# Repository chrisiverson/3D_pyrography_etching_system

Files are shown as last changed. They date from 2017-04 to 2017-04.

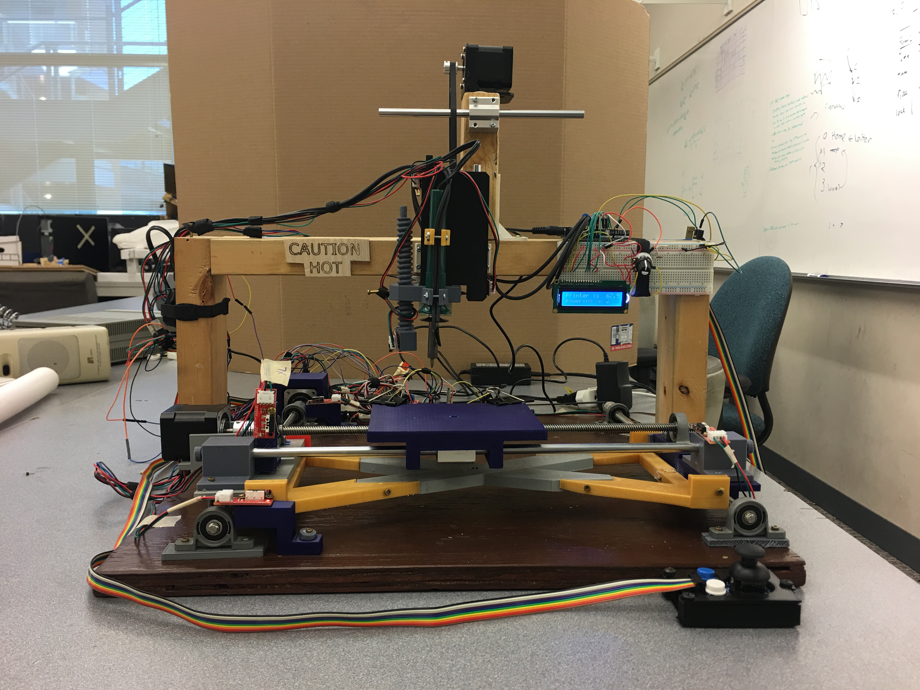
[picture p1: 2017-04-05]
Pictures/IMG_1217.JPG

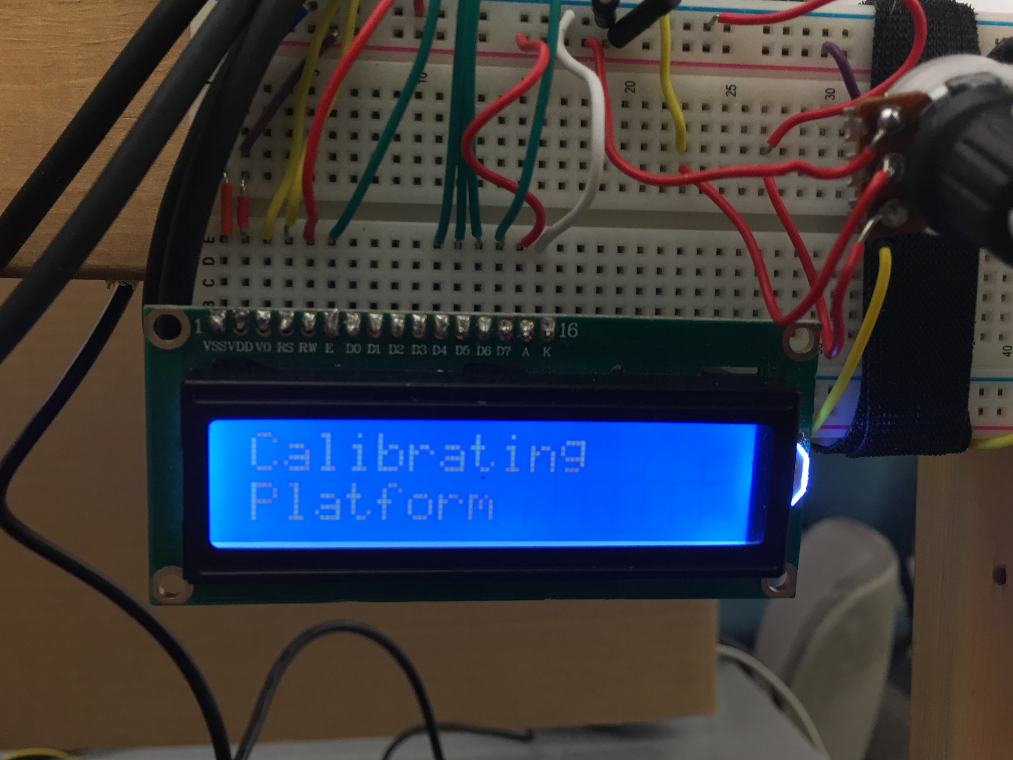
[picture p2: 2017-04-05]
Pictures/IMG_1232.JPG

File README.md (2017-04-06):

# 3D_pyrography_etching_system

3.P.E.S is a pyrography etching system. This system is capable of wood burning an image that the  user manually engraves via a joystick or sends to our machine via a smartphone application. The reason  we designed this system is because of our interest in 3-D printing. We wanted to take an artistic and unique approach to implementing an x, y, z theta platform.

Video demo: https://www.youtube.com/watch?v=G6UNE0NW478

This project falls under creative copyrights to 

Christopher Iverson
chris.iverson.ee@gmail.com

Dineth Gamalath
dinethgamalath@gmail.com

Steven Hernandez
stevenhdz@gmail.com

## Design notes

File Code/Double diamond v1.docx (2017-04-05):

/*

2-axis joystick connected to an Arduino Micro

to output 4 pins, up, down, left & right

If you are using pull down resistors, change all the HIGHs to LOWs and LOWs to HIGH.

This skectch is using pull up resistors.

*/

String readString;

int UD = 0;

int LR = 0;

/* Arduino Micro output pins*/

int DWN = 27;

int UP = 29;

int LEFT = 31;

int RT = 33;

/* Arduino Micro Input Pins */

int IUP=59;//A5

int ILR=63;//A9

int MID = 33; // 33 mid point delta arduino, use 4 for attiny

int LRMID = 0;

int UPMID = 0;

char randomflag = 0;

const int x_endstopPin_min = 3; // endstop for x-axis (min)

const int x_endstopPin_max = 2; // endstop for x-axis (max)

const int y_endstopPin_min = 14; // endstop for y-axis (min)

const int y_endstopPin_max = 15; // endstop for y-axis (max)

const int z_endstopPin = 18; //endstop for z-axis

const int buttonPin = 47; //D47 // the number of the pushbutton pin

const int buttonPin2 = 32; //D32

const int ledPin = 23; // the number of the LED pin

int buttonState = 0; // variable for reading the pushbutton status

int buttonState2 = 0;

int x_endstopState_min = 0; //these states will contain value from reading input values

int x_endstopState_max = 0;

int y_endstopState_min = 0;

int y_endstopState_max = 0;

int z_endstopState = 0;

int XL = 0;

int XR = 0;

int YU = 0;

int YD = 0;

int ZU = 0;

int ZD = 0;

int XL1 = 1000;

int XR1 = 0;

int YU1 = 0;

int YD1 = 1000;

int ZU1 = 0;

int ZD1 = 0;

int XL2 = 0;

int XR2 = 1000;

int YU2 = 0;

int YD2 = 1000;

int ZU2 = 0;

int ZD2 = 0;

int XL3 = 1000;

int XR3 = 0;

int YU3 = 0;

int YD3 = 1000;

int ZU3 = 0;

int ZD3 = 0;

int XL4 = 0;

int XR4 = 1000;

int YU4 = 0;

int YD4 = 1500;

int ZU4 = 0;

int ZD4 = 0;

int XL5 = 0;

int XR5 = 1000;

int YU5 = 1000;

int YD5 = 0;

int ZU5 = 0;

int ZD5 = 0;

int XL6 = 1000;

int XR6 = 0;

int YU6 = 1000;

int YD6 = 0;

int ZU6 = 0;

int ZD6 = 0;

int XL7 = 0;

int XR7 = 1000;

int YU7 = 1000;

int YD7 = 0;

int ZU7 = 0;

int ZD7 = 0;

int XL8 = 1000;

int XR8 = 0;

int YU8 = 1000;

int YD8 = 0;

int ZU8 = 0;

int ZD8 = 0;

int XLEND = 0;

int XREND = 0;

int YUEND = 0;

int YDEND = 0;

int ZUEND = 0;

int ZDEND = 0;

int Done = 1;

int move_num = 0;

void mover()

{

Done = 0;

XL = XL1;

XR = XR1;

YU = YU1;

YD = YD1;

ZU = ZU1;

ZD = ZD1;

XL1 = XL2;

XR1 = XR2;

YU1 = YU2;

YD1 = YD2;

ZU1 = ZU2;

ZD1 = ZD2;

XL2 = XL3;

XR2 = XR3;

YU2 = YU3;

YD2 = YD3;

ZU2 = ZU3;

ZD2 = ZD3;

XL3 = XL4;

XR3 = XR4;

YU3 = YU4;

YD3 = YD4;

ZU3 = ZU4;

ZD3 = ZD4;

XL4 = XL5;

XR4 = XR5;

YU4 = YU5;

YD4 = YD5;

ZU4 = ZU5;

ZD4 = ZD5;

XL5 = XL6;

XR5 = XR6;

YU5 = YU6;

YD5 = YD6;

ZU5 = ZU6;

ZD5 = ZD6;

XL6 = XL7;

XR6 = XR7;

YU6 = YU7;

YD6 = YD7;

ZU6 = ZU7;

ZD6 = ZD7;

XL7 = XL8;

XR7 = XR8;

YU7 = YU8;

YD7 = YD8;

ZU7 = ZU8;

ZD7 = ZD8;

XL8 = XLEND;

XR8 = XREND;

YU8 = YUEND;

YD8 = YDEND;

ZU8 = ZUEND;

ZD8 = ZDEND;

move_num++;

return;

}

void setup(){

Serial.begin(9600);

pinMode(ledPin, OUTPUT);

// initialize the pushbutton pin as an input:

pinMode(buttonPin, INPUT);

pinMode(x_endstopPin_min, INPUT);

pinMode(x_endstopPin_max, INPUT);

pinMode(y_endstopPin_min, INPUT);

pinMode(y_endstopPin_max, INPUT);

pinMode(z_endstopPin, INPUT);

pinMode(DWN, OUTPUT);

pinMode(UP, OUTPUT);

pinMode(LEFT, OUTPUT);

pinMode(RT, OUTPUT);

digitalWrite(DWN, HIGH);

digitalWrite(UP, HIGH);

digitalWrite(LEFT, HIGH);

digitalWrite(RT, HIGH);

//calabrate center

LRMID = analogRead(ILR);

UPMID = analogRead(IUP);

pinMode(38, OUTPUT); //Enable X // old 6

pinMode(54, OUTPUT); //Step X // old 5

pinMode(55, OUTPUT); //Direction // old 4

pinMode(56, OUTPUT);// Enable Y

pinMode(60, OUTPUT);// Step Y

pinMode(61, OUTPUT);// Direction Y

//digitalWrite(38,LOW);

pinMode(62, OUTPUT);// Enable Z

pinMode(46, OUTPUT);// Step Z

pinMode(48, OUTPUT);// Direction Z

}

void loop(){

while (Serial.available()) {

delay(3);

char c = Serial.read();

readString += c;

}

//***********************************BLUETOOTH BEGIN*****************

if (readString.length() >0) {

Serial.println(readString);

if(readString == "UP")

{

randomflag = 1;

}

else if (readString == "off")

{

randomflag = 0;

}

readString="";

}

//***********************************BLUETOOTH END*******************

x_endstopState_min = digitalRead(x_endstopPin_min); //this obtains the "1" or "0" from endstop signal

x_endstopState_max = digitalRead(x_endstopPin_max);

y_endstopState_min = digitalRead(y_endstopPin_min);

y_endstopState_max = digitalRead(y_endstopPin_max);

z_endstopState = digitalRead(z_endstopPin);

buttonState = digitalRead(buttonPin);

buttonState2 = digitalRead(buttonPin2);

UD = analogRead(IUP);

LR = analogRead(ILR);

//z-direction button UP

int buttonvar = buttonState;

int buttonvar2 = buttonState2;

int x_endstopvar_min = x_endstopState_min;

int x_endstopvar_max = x_endstopState_max;

int y_endstopvar_min = y_endstopState_min;

int y_endstopvar_max = y_endstopState_max;

int z_endstopvar = z_endstopState;

if (!buttonvar)

{

// turn LED on:

digitalWrite(48,LOW);//direction

digitalWrite(46,HIGH);//step

digitalWrite(46,LOW);//step

delayMicroseconds(200);

}

else if(buttonvar)

{

digitalWrite(46,LOW);

}

if (!buttonvar2 && z_endstopvar)

{

// turn LED on:

digitalWrite(ledPin, HIGH);

// Serial.println("LED on");

digitalWrite(48,HIGH);//direction

digitalWrite(46,HIGH);//step

digitalWrite(46,LOW);//step

delayMicroseconds(200);

}

else if(buttonvar || buttonvar2)

{

digitalWrite(46,LOW);

}

if (Done && (move_num < 9))

{

mover();

}

if ( XR == 0 && XL == 0 && YU == 0 && YD == 0)

{

//Serial.println("TESTEHRFSB");

Done = 1;

}

// y-direction UP

if((((UD < UPMID - MID) || (randomflag ==1)) || (YU > 0)) && y_endstopvar_min ){

digitalWrite(DWN, LOW);

digitalWrite(61,LOW);

digitalWrite(UP, LOW);

digitalWrite(60,HIGH);

delayMicroseconds(200);

YU--;

}

else

{

digitalWrite(DWN, HIGH);

digitalWrite(60,LOW);

}

// y-direction DOWN

if(((UD > UPMID + MID) || (YD > 0)) && y_endstopvar_max ){

digitalWrite(UP, LOW);

digitalWrite(61,HIGH);

//digitalWrite(DWN, LOW);

digitalWrite(60,HIGH);

delayMicroseconds(200);

YD--;

}

else

{

digitalWrite(UP, HIGH);

digitalWrite(60,LOW);

}

// LEFT-RIGHT

//x-direciton LEFT

if(((LR < LRMID - MID) || (XL > 0)) && x_endstopvar_max ){// min

digitalWrite(55,LOW);

//digitalWrite(LEFT, LOW);// LEDS

digitalWrite(54,HIGH);

delayMicroseconds(200);

XL--;

}

else{

digitalWrite(54,LOW);

digitalWrite(LEFT, HIGH);

}

//x-direction RIGHT

if(((LR > LRMID + MID) || (XR > 0)) && x_endstopvar_min ){

digitalWrite(55,HIGH);

//digitalWrite(RT, LOW);

digitalWrite(54,HIGH);

delayMicroseconds(200);

XR--;

}else{

digitalWrite(54,LOW);

digitalWrite(RT, HIGH);

}

/*

//x-direciton LEFT

if(LR < LRMID - MID){

digitalWrite(48,LOW);

digitalWrite(LEFT, LOW);

digitalWrite(46,HIGH);

delayMicroseconds(200);

}

else{

digitalWrite(46,LOW);

digitalWrite(LEFT, HIGH);

}

//x-direction RIGHT

if(LR > LRMID + MID){

digitalWrite(48,HIGH);

digitalWrite(RT, LOW);

digitalWrite(46,HIGH);

delayMicroseconds(200);

}else{

digitalWrite(46,LOW);

digitalWrite(RT, HIGH);

}

*/

//delay(200);

}

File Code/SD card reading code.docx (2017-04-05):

File dataFile = SD.open("Strip3_5.txt"); if (datafile) { for (index = 0; index <= 9; index++) { int input = datafile.parseInt(); String3_5[index] = input; Serial.println(input); } file.close(); }

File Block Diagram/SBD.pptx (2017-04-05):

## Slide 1

System Block Diagram for EDWARD

Drill / Soldering Attachment / Pen

End Stops / Sensors

Arduino 1

Arduino Shield Driver Board + Driver

X – Direction Stepper Motor

Joystick

Y – Direction Stepper Motor

Z – Direction Stepper Motor

Application

Wireless Communication Module

Arduino 2

Voltage & Power Controller

Display Unit

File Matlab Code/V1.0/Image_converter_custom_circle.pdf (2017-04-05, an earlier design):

clc
clear all
close all

Im_name = 'custom.png';
Im = imread(Im_name);
Im_size(:)=size(Im);%Gather size data of image X=Im_size(1);%Save the x dimension Y=Im_size(2);%Save the Y dimension

while Y > 300
Im = imresize(Im,.5);
Im_size(:)=size(Im);%Gather size data of image X=Im_size(1)%Save the x dimension Y=Im_size(2)%Save the Y dimension
end

X = 450
Y = 481
X = 225
Y = 241

histogram(Im)

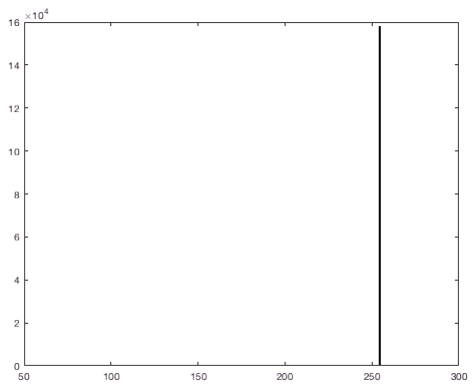
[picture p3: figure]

%Add or remove thresholds in the line below according to the histogram %Globe threshs: 0,117,200
thresh = [117,200]

thresh =

117 200

%Convert the image based on the thresholds Im_Shaded = imquantize(Im,thresh);

%fileID = fopen('Untitled.txt','wt'); %fprintf(fileID,'%f',Im_Shaded); %fclose(fileID);

imshow(Im);

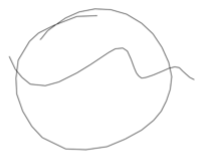
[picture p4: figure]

histogram(Im)

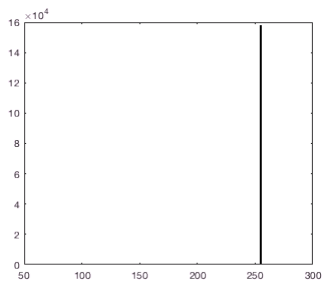
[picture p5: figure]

histogram(Im_Shaded)

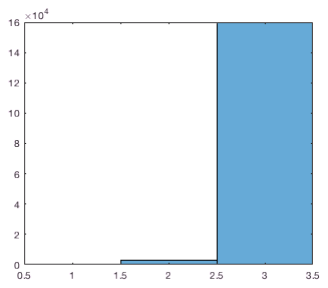
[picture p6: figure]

imshow(Im_Shaded,[])

%Now isolating each shade as a seperate b and w image max_value=max(Im_Shaded(:))

max_value = 3

Im_array_1=im2bw(Im,thresh(1)/255); Im_array_2=~im2bw(Im,thresh(2)/255); Im_array_3=im2bw(Im,thresh(2)/255);

imshow(Im_array_1);

imshow(Im_array_2);

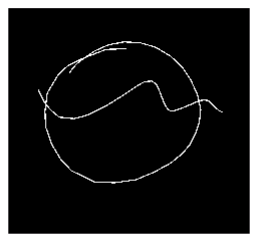
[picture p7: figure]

imshow(Im_array_3);

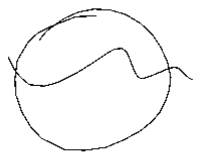
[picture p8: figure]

%-------------------------------------------num_objects_1 = max(max(bwlabel(Im_array_1)))

num_objects_1 = 1

num_objects_2 = max(max(bwlabel(Im_array_2)))

num_objects_2 = 1

num_objects_3 = max(max(bwlabel(Im_array_3)))

num_objects_3 = 1

%Converts the different shades into outlines
Im_array_outline_3 = bwmorph(Im_array_3,'remove');
Im_array_outline_2 = (bwmorph(bwmorph(Im_array_2,'remove'),'clean'));
Im_array_outline_1 = bwmorph(Im_array_1,'remove')-bwmorph(Im_array_3,'remove')-bwmorph(Im_array_2,'remove');

imshow(Im_array_outline_1)

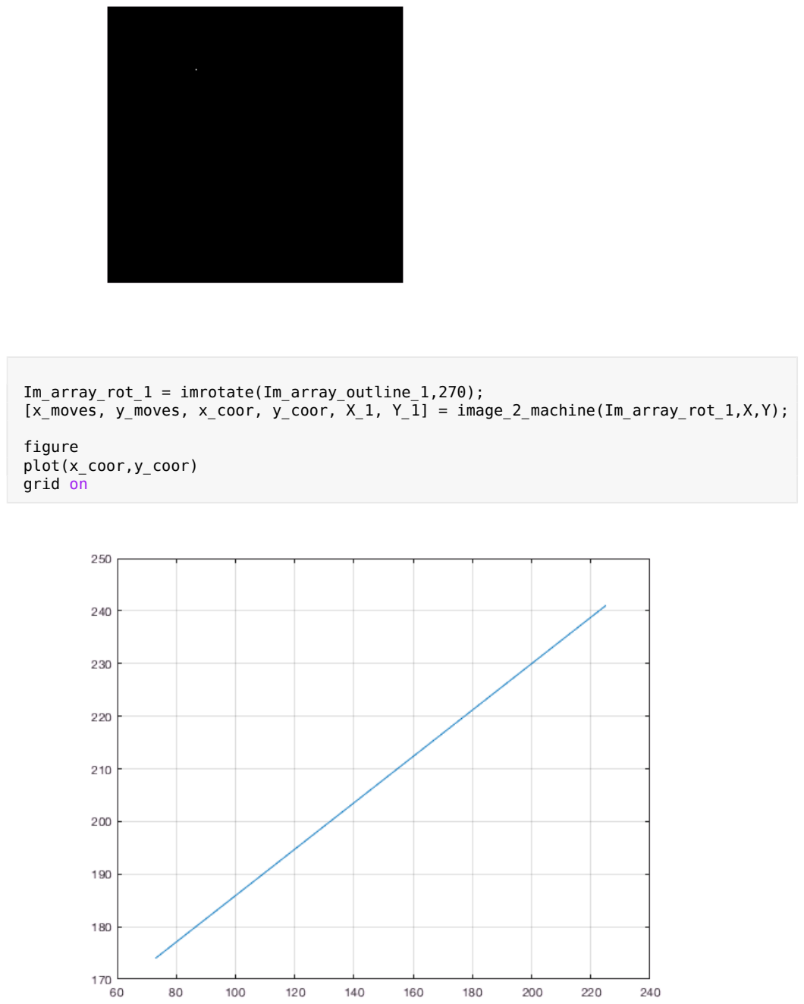
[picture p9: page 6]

Im_array_rot_1 = imrotate(Im_array_outline_1,270);
[x_moves, y_moves, x_coor, y_coor, X_1, Y_1] = image_2_machine(Im_array_rot_1,X,Y);

figure
plot(x_coor,y_coor)
grid on

Im_please_work = Im_array_1 - Im_array_3 - Im_array_outline_2;

imshow(Im_please_work)

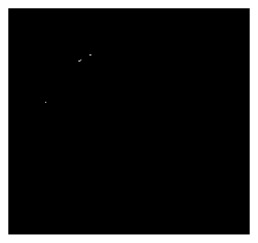
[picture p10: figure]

Im_array_rot_1 = imrotate(Im_please_work,270);
[x_moves_2, y_moves_2, x_coor_2, y_coor_2, X_2, Y_2] = image_2_machine(Im_array_rot_1,X_1,Y_1);

figure
plot(x_coor_2,y_coor_2)
grid on

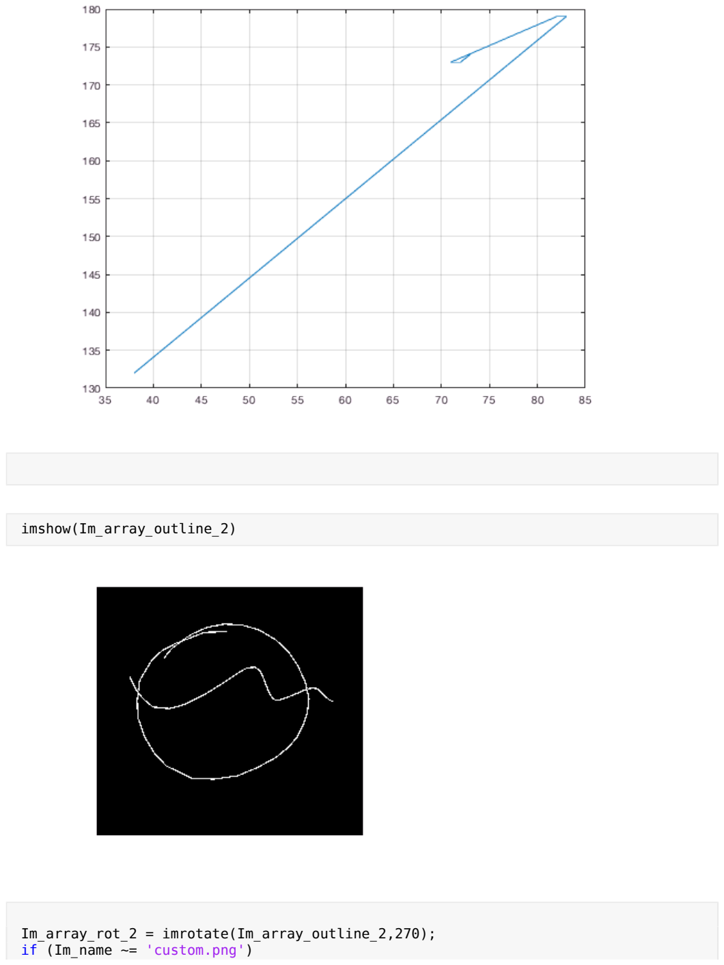
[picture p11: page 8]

imshow(Im_array_outline_2)

Im_array_rot_2 = imrotate(Im_array_outline_2,270); if (Im_name ~= 'custom.png')

[x_moves_3, y_moves_3, x_coor_3, y_coor_3, X_3, Y_3] = image_2_machine(Im_array_rot_2,X_2,Y_2); else
[x_moves_3, y_moves_3, x_coor_3, y_coor_3, X_3, Y_3] = image_2_machine(Im_array_rot_2,1,1); end

figure
plot(x_coor_3,y_coor_3)
grid on

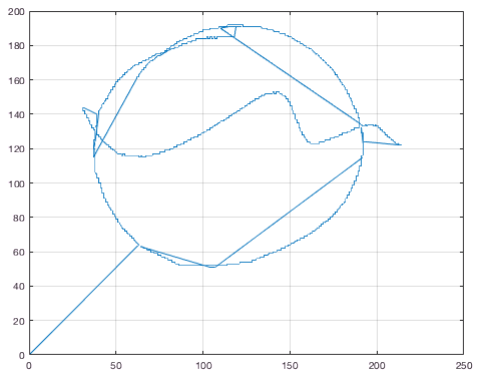
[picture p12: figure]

Im_please_work_2 = Im_array_2-Im_array_1;

imshow(Im_please_work_2)

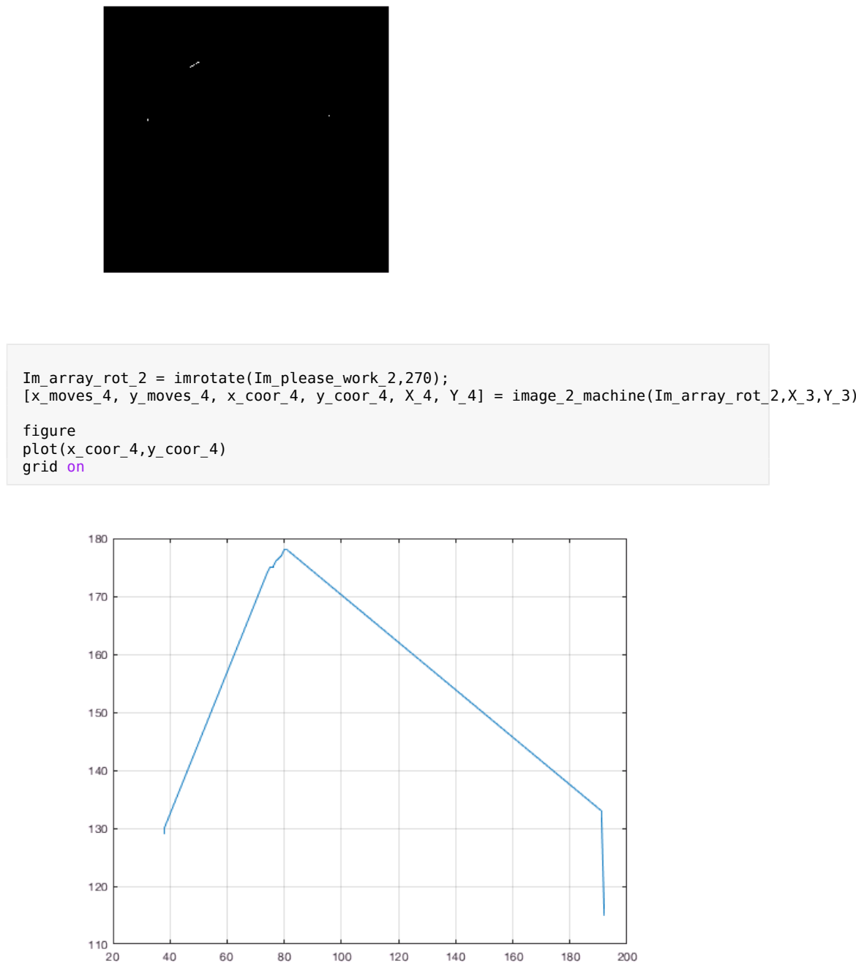
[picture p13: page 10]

Im_array_rot_2 = imrotate(Im_please_work_2,270);
[x_moves_4, y_moves_4, x_coor_4, y_coor_4, X_4, Y_4] = image_2_machine(Im_array_rot_2,X_3,Y_3);

figure
plot(x_coor_4,y_coor_4)
grid on dec2bin(abs(y_moves_3(1)),8);

%[x_move_3, y_move_3, final_x_3, final_y_3, num_steps_3 ] = conv_to_moves( Im_array_outline_1, final_x_2, final_y_2);

if (Im_name ~= 'custom.png')
num_steps = length(x_moves_4)+length(x_moves_3)+length(x_moves_2)+length(x_moves)

fileID = fopen('image_data.h','w');
fprintf(fileID,'long num_of_steps = ');
fprintf(fileID,'%1i;\n\n',num_steps);
fprintf(fileID,'//Coordinates: \n//'); for i = 1:length(x_coor_3)
if x_coor_3(i) < 0
fprintf(fileID,'%1i',0-x_coor_3(i)); else
fprintf(fileID,'%1i',x_coor_3(i)); end
fprintf(fileID,',');
if y_coor_3(i) < 0
fprintf(fileID,'%1i',0-y_coor_3(i)); else
fprintf(fileID,'%1i',y_coor_3(i)); end
if (num_steps ~= i)

fprintf(fileID,',');
end
end

fprintf(fileID,'\n//Move list from origin (0,0) with every 4 numbers being a step: \n//'); for i = 1:length(x_moves_3)
if x_moves_3(i) < 0
fprintf(fileID,' %1i, 0',0-x_moves_3(i));
else
fprintf(fileID,' 0, %1i',x_moves_3(i)); end
fprintf(fileID,',');
if y_moves_3(i) < 0
fprintf(fileID,' %1i, 0',0-y_moves_3(i)); else
fprintf(fileID,' 0, %1i',y_moves_3(i)); end
if (num_steps ~= i)

fprintf(fileID,';');
end
end
fprintf(fileID,'\n//Binary move list with 3 moves per byte\n//Format: 0x00,Move1,Move2,Move3\n//Example: 0x00110010 = 0x00,UR,DL,UL\n'); fprintf(fileID,'byte move_list[] = {');

write_2_file(x_moves_3,y_moves_3,fileID,1)
fprintf(fileID,'\n');
write_2_file(x_moves,y_moves,fileID,0) fprintf(fileID,'\n');
write_2_file(x_moves_2,y_moves_2,fileID,0) fprintf(fileID,'\n');
write_2_file(x_moves_4,y_moves_4,fileID,0) fprintf(fileID,'};');

fclose(fileID);

type image_data.h

else
num_steps = length(x_moves_3)

fileID = fopen('image_data.h','w'); fprintf(fileID,'long num_of_steps = '); fprintf(fileID,'%1i;\n\n',num_steps);

fprintf(fileID,'char move_list['); fprintf(fileID,'] = {');

for i = 1:num_steps
if x_moves_3(i) < 0
fprintf(fileID,' %1i, 0',0-x_moves_3(i)); else
fprintf(fileID,' 0, %1i',x_moves_3(i)); end
fprintf(fileID,',');
if y_moves_3(i) < 0
fprintf(fileID,' %1i, 0',0-y_moves_3(i)); else
fprintf(fileID,' 0, %1i',y_moves_3(i)); end
if (num_steps ~= i)

fprintf(fileID,',');
end
end

fprintf(fileID,'};\n//Fin'); fprintf(fileID,'\n');
fclose(fileID);

type image_data.h
end

num_steps = 915
long num_of_steps = 915;

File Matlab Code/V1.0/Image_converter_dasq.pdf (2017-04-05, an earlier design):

clc
clear all
close all

Im_name = 'custom.png';
Im = imread(Im_name);
Im_size(:)=size(Im);%Gather size data of image X=Im_size(1);%Save the x dimension Y=Im_size(2);%Save the Y dimension

while Y > 300
Im = imresize(Im,.5);
Im_size(:)=size(Im);%Gather size data of image X=Im_size(1)%Save the x dimension Y=Im_size(2)%Save the Y dimension
end

X = 450
Y = 481
X = 225
Y = 241

histogram(Im)

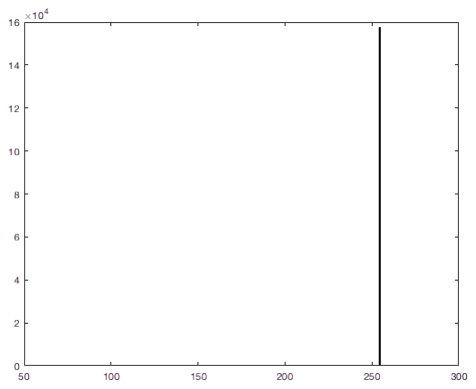
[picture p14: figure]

%Add or remove thresholds in the line below according to the histogram %Globe threshs: 0,117,200
thresh = [117,200]

thresh =

117 200

%Convert the image based on the thresholds Im_Shaded = imquantize(Im,thresh);

%fileID = fopen('Untitled.txt','wt'); %fprintf(fileID,'%f',Im_Shaded); %fclose(fileID);

imshow(Im);

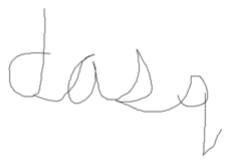
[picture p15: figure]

histogram(Im)


histogram(Im_Shaded)


imshow(Im_Shaded,[])

%Now isolating each shade as a seperate b and w image max_value=max(Im_Shaded(:))

max_value = 3

Im_array_1=im2bw(Im,thresh(1)/255); Im_array_2=~im2bw(Im,thresh(2)/255); Im_array_3=im2bw(Im,thresh(2)/255);

imshow(Im_array_1);

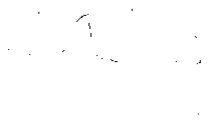
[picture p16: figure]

imshow(Im_array_2);

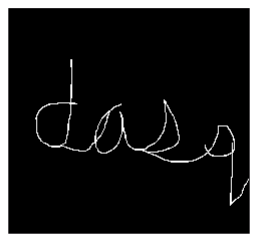
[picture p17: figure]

imshow(Im_array_3);

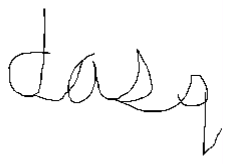
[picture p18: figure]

%-------------------------------------------num_objects_1 = max(max(bwlabel(Im_array_1)))

num_objects_1 = 1

num_objects_2 = max(max(bwlabel(Im_array_2)))

num_objects_2 = 1

num_objects_3 = max(max(bwlabel(Im_array_3)))

num_objects_3 = 1

%Converts the different shades into outlines
Im_array_outline_3 = bwmorph(Im_array_3,'remove');
Im_array_outline_2 = (bwmorph(bwmorph(Im_array_2,'remove'),'clean'));
Im_array_outline_1 = bwmorph(Im_array_1,'remove')-bwmorph(Im_array_3,'remove')-bwmorph(Im_array_2,'remove');

imshow(Im_array_outline_1)

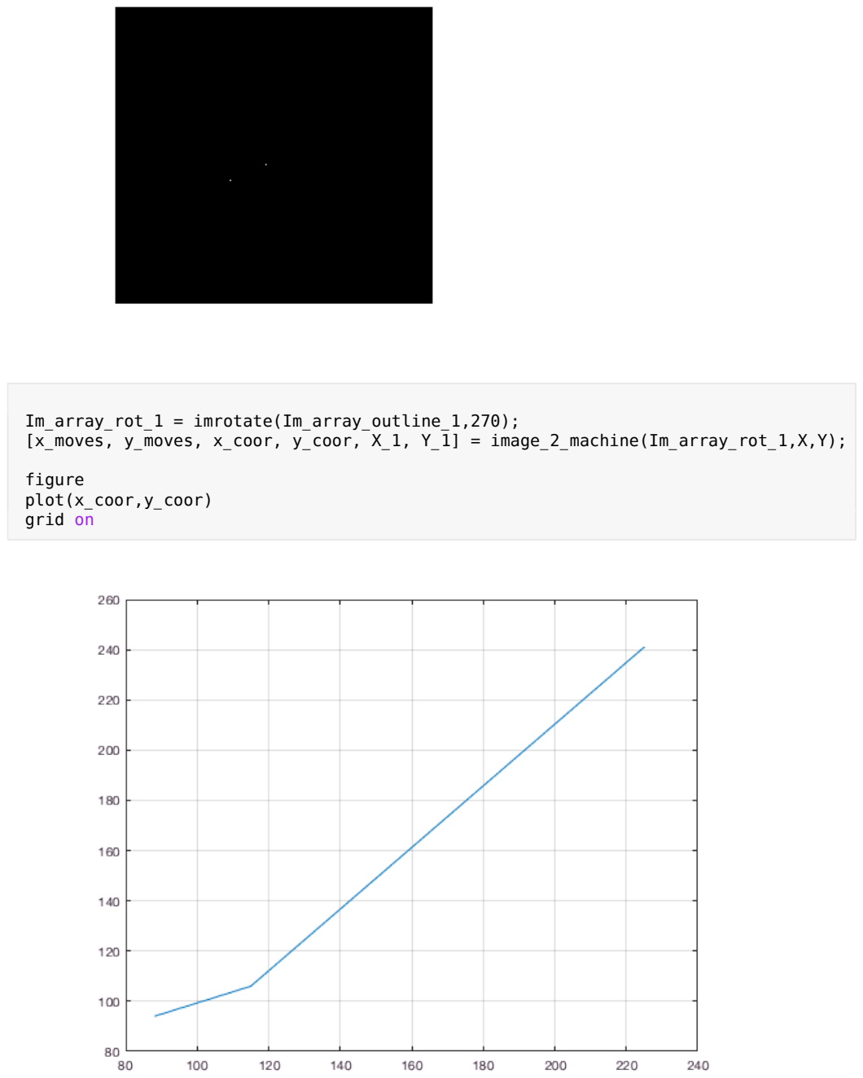
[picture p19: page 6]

Im_array_rot_1 = imrotate(Im_array_outline_1,270);
[x_moves, y_moves, x_coor, y_coor, X_1, Y_1] = image_2_machine(Im_array_rot_1,X,Y);

figure
plot(x_coor,y_coor)
grid on

Im_please_work = Im_array_1 - Im_array_3 - Im_array_outline_2;

imshow(Im_please_work)

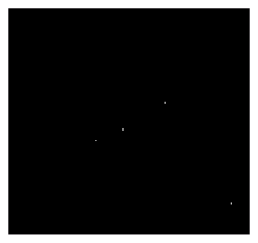
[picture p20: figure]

Im_array_rot_1 = imrotate(Im_please_work,270);
[x_moves_2, y_moves_2, x_coor_2, y_coor_2, X_2, Y_2] = image_2_machine(Im_array_rot_1,X_1,Y_1);

figure
plot(x_coor_2,y_coor_2)
grid on

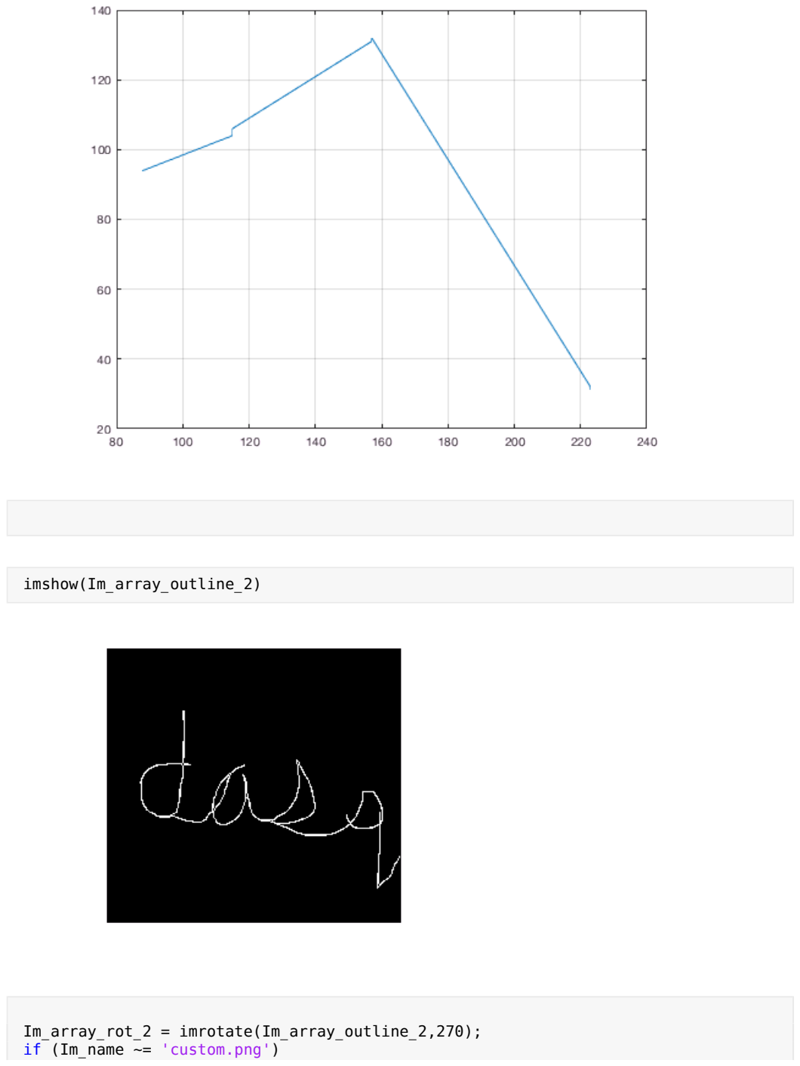
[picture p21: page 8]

imshow(Im_array_outline_2)

Im_array_rot_2 = imrotate(Im_array_outline_2,270); if (Im_name ~= 'custom.png')

[x_moves_3, y_moves_3, x_coor_3, y_coor_3, X_3, Y_3] = image_2_machine(Im_array_rot_2,X_2,Y_2); else
[x_moves_3, y_moves_3, x_coor_3, y_coor_3, X_3, Y_3] = image_2_machine(Im_array_rot_2,1,1); end

figure
plot(x_coor_3,y_coor_3)
grid on

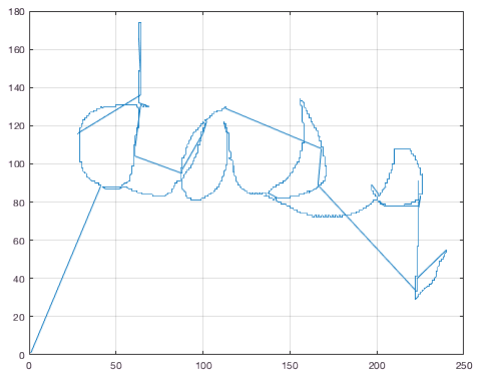
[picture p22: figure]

Im_please_work_2 = Im_array_2-Im_array_1;

imshow(Im_please_work_2)

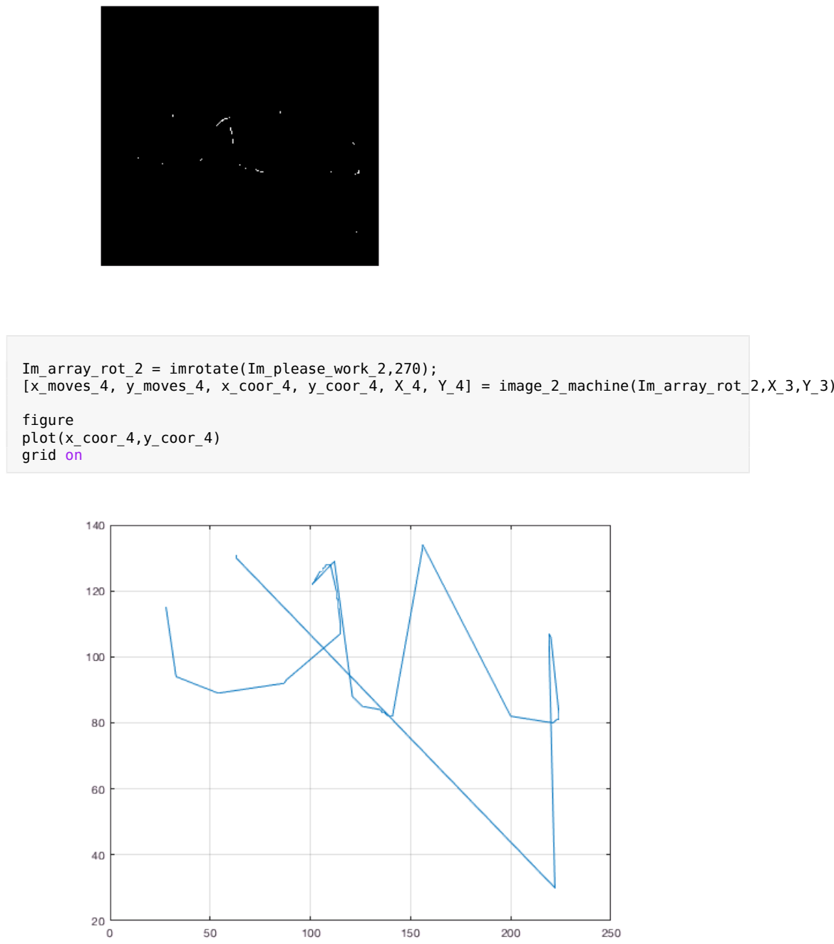
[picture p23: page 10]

Im_array_rot_2 = imrotate(Im_please_work_2,270);
[x_moves_4, y_moves_4, x_coor_4, y_coor_4, X_4, Y_4] = image_2_machine(Im_array_rot_2,X_3,Y_3);

figure
plot(x_coor_4,y_coor_4)
grid on dec2bin(abs(y_moves_3(1)),8);

%[x_move_3, y_move_3, final_x_3, final_y_3, num_steps_3 ] = conv_to_moves( Im_array_outline_1, final_x_2, final_y_2);

if (Im_name ~= 'custom.png')
num_steps = length(x_moves_4)+length(x_moves_3)+length(x_moves_2)+length(x_moves)

fileID = fopen('image_data.h','w');
fprintf(fileID,'long num_of_steps = ');
fprintf(fileID,'%1i;\n\n',num_steps);
fprintf(fileID,'//Coordinates: \n//'); for i = 1:length(x_coor_3)
if x_coor_3(i) < 0
fprintf(fileID,'%1i',0-x_coor_3(i)); else
fprintf(fileID,'%1i',x_coor_3(i)); end
fprintf(fileID,',');
if y_coor_3(i) < 0
fprintf(fileID,'%1i',0-y_coor_3(i)); else
fprintf(fileID,'%1i',y_coor_3(i)); end
if (num_steps ~= i)

fprintf(fileID,',');
end
end

fprintf(fileID,'\n//Move list from origin (0,0) with every 4 numbers being a step: \n//'); for i = 1:length(x_moves_3)
if x_moves_3(i) < 0
fprintf(fileID,' %1i, 0',0-x_moves_3(i));
else
fprintf(fileID,' 0, %1i',x_moves_3(i)); end
fprintf(fileID,',');
if y_moves_3(i) < 0
fprintf(fileID,' %1i, 0',0-y_moves_3(i)); else
fprintf(fileID,' 0, %1i',y_moves_3(i)); end
if (num_steps ~= i)

fprintf(fileID,';');
end
end
fprintf(fileID,'\n//Binary move list with 3 moves per byte\n//Format: 0x00,Move1,Move2,Move3\n//Example: 0x00110010 = 0x00,UR,DL,UL\n'); fprintf(fileID,'byte move_list[] = {');

write_2_file(x_moves_3,y_moves_3,fileID,1)
fprintf(fileID,'\n');
write_2_file(x_moves,y_moves,fileID,0) fprintf(fileID,'\n');
write_2_file(x_moves_2,y_moves_2,fileID,0) fprintf(fileID,'\n');
write_2_file(x_moves_4,y_moves_4,fileID,0) fprintf(fileID,'};');

fclose(fileID);

type image_data.h

else
num_steps = length(x_moves_3)

fileID = fopen('image_data.h','w'); fprintf(fileID,'long num_of_steps = '); fprintf(fileID,'%1i;\n\n',num_steps);

fprintf(fileID,'char move_list['); fprintf(fileID,'] = {');

for i = 1:num_steps
if x_moves_3(i) < 0
fprintf(fileID,' %1i, 0',0-x_moves_3(i)); else
fprintf(fileID,' 0, %1i',x_moves_3(i)); end
fprintf(fileID,',');
if y_moves_3(i) < 0
fprintf(fileID,' %1i, 0',0-y_moves_3(i)); else
fprintf(fileID,' 0, %1i',y_moves_3(i)); end
if (num_steps ~= i)

fprintf(fileID,',');
end
end

fprintf(fileID,'};\n//Fin'); fprintf(fileID,'\n');
fclose(fileID);

type image_data.h
end

num_steps = 1009
long num_of_steps = 1009;

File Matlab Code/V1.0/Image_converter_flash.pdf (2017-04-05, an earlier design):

clc
clear all
close all

Im_name = 'custom.png';
Im = imread(Im_name);
Im_size(:)=size(Im);%Gather size data of image X=Im_size(1);%Save the x dimension Y=Im_size(2);%Save the Y dimension

while Y > 300
Im = imresize(Im,.5);
Im_size(:)=size(Im);%Gather size data of image X=Im_size(1)%Save the x dimension Y=Im_size(2)%Save the Y dimension
end

X = 450
Y = 481
X = 225
Y = 241

histogram(Im)

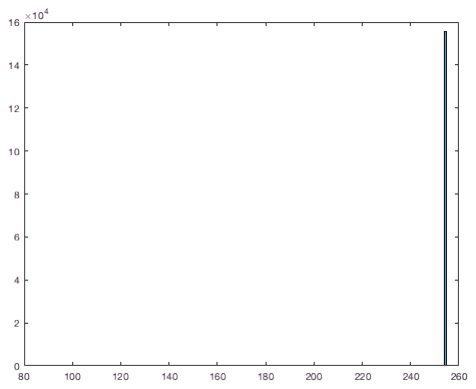
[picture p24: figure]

%Add or remove thresholds in the line below according to the histogram %Globe threshs: 0,117,200
thresh = [117,200]

thresh =

117 200

%Convert the image based on the thresholds Im_Shaded = imquantize(Im,thresh);

%fileID = fopen('Untitled.txt','wt'); %fprintf(fileID,'%f',Im_Shaded); %fclose(fileID);

imshow(Im);

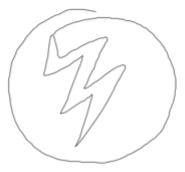
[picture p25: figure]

histogram(Im)

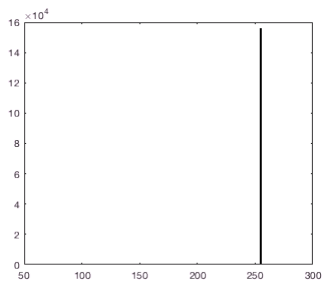
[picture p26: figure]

histogram(Im_Shaded)


imshow(Im_Shaded,[])

%Now isolating each shade as a seperate b and w image max_value=max(Im_Shaded(:))

max_value = 3

Im_array_1=im2bw(Im,thresh(1)/255); Im_array_2=~im2bw(Im,thresh(2)/255); Im_array_3=im2bw(Im,thresh(2)/255);

imshow(Im_array_1);

imshow(Im_array_2);


imshow(Im_array_3);


%-------------------------------------------num_objects_1 = max(max(bwlabel(Im_array_1)))

num_objects_1 = 1

num_objects_2 = max(max(bwlabel(Im_array_2)))

num_objects_2 = 1

num_objects_3 = max(max(bwlabel(Im_array_3)))

num_objects_3 = 1

%Converts the different shades into outlines
Im_array_outline_3 = bwmorph(Im_array_3,'remove');
Im_array_outline_2 = (bwmorph(bwmorph(Im_array_2,'remove'),'clean'));
Im_array_outline_1 = bwmorph(Im_array_1,'remove')-bwmorph(Im_array_3,'remove')-bwmorph(Im_array_2,'remove');

imshow(Im_array_outline_1)


Im_array_rot_1 = imrotate(Im_array_outline_1,270);
[x_moves, y_moves, x_coor, y_coor, X_1, Y_1] = image_2_machine(Im_array_rot_1,X,Y);

figure
plot(x_coor,y_coor)
grid on

Im_please_work = Im_array_1 - Im_array_3 - Im_array_outline_2;

imshow(Im_please_work)


Im_array_rot_1 = imrotate(Im_please_work,270);
[x_moves_2, y_moves_2, x_coor_2, y_coor_2, X_2, Y_2] = image_2_machine(Im_array_rot_1,X_1,Y_1);

figure
plot(x_coor_2,y_coor_2)
grid on


imshow(Im_array_outline_2)

Im_array_rot_2 = imrotate(Im_array_outline_2,270); if (Im_name ~= 'custom.png')

[x_moves_3, y_moves_3, x_coor_3, y_coor_3, X_3, Y_3] = image_2_machine(Im_array_rot_2,X_2,Y_2); else
[x_moves_3, y_moves_3, x_coor_3, y_coor_3, X_3, Y_3] = image_2_machine(Im_array_rot_2,1,1); end

figure
plot(x_coor_3,y_coor_3)
grid on


Im_please_work_2 = Im_array_2-Im_array_1;

imshow(Im_please_work_2)


Im_array_rot_2 = imrotate(Im_please_work_2,270);
[x_moves_4, y_moves_4, x_coor_4, y_coor_4, X_4, Y_4] = image_2_machine(Im_array_rot_2,X_3,Y_3);

figure
plot(x_coor_4,y_coor_4)
grid on dec2bin(abs(y_moves_3(1)),8);

%[x_move_3, y_move_3, final_x_3, final_y_3, num_steps_3 ] = conv_to_moves( Im_array_outline_1, final_x_2, final_y_2);

if (Im_name ~= 'custom.png')
num_steps = length(x_moves_4)+length(x_moves_3)+length(x_moves_2)+length(x_moves)

fileID = fopen('image_data.h','w');
fprintf(fileID,'long num_of_steps = ');
fprintf(fileID,'%1i;\n\n',num_steps);
fprintf(fileID,'//Coordinates: \n//'); for i = 1:length(x_coor_3)
if x_coor_3(i) < 0
fprintf(fileID,'%1i',0-x_coor_3(i)); else
fprintf(fileID,'%1i',x_coor_3(i)); end
fprintf(fileID,',');
if y_coor_3(i) < 0
fprintf(fileID,'%1i',0-y_coor_3(i)); else
fprintf(fileID,'%1i',y_coor_3(i)); end
if (num_steps ~= i)

fprintf(fileID,',');
end
end

fprintf(fileID,'\n//Move list from origin (0,0) with every 4 numbers being a step: \n//'); for i = 1:length(x_moves_3)
if x_moves_3(i) < 0
fprintf(fileID,' %1i, 0',0-x_moves_3(i));
else
fprintf(fileID,' 0, %1i',x_moves_3(i)); end
fprintf(fileID,',');
if y_moves_3(i) < 0
fprintf(fileID,' %1i, 0',0-y_moves_3(i)); else
fprintf(fileID,' 0, %1i',y_moves_3(i)); end
if (num_steps ~= i)

fprintf(fileID,';');
end
end
fprintf(fileID,'\n//Binary move list with 3 moves per byte\n//Format: 0x00,Move1,Move2,Move3\n//Example: 0x00110010 = 0x00,UR,DL,UL\n'); fprintf(fileID,'byte move_list[] = {');

write_2_file(x_moves_3,y_moves_3,fileID,1)
fprintf(fileID,'\n');
write_2_file(x_moves,y_moves,fileID,0) fprintf(fileID,'\n');
write_2_file(x_moves_2,y_moves_2,fileID,0) fprintf(fileID,'\n');
write_2_file(x_moves_4,y_moves_4,fileID,0) fprintf(fileID,'};');

fclose(fileID);

type image_data.h

else
num_steps = length(x_moves_3)

fileID = fopen('image_data.h','w'); fprintf(fileID,'long num_of_steps = '); fprintf(fileID,'%1i;\n\n',num_steps);

fprintf(fileID,'char move_list['); fprintf(fileID,'] = {');

for i = 1:num_steps
if x_moves_3(i) < 0
fprintf(fileID,' %1i, 0',0-x_moves_3(i)); else
fprintf(fileID,' 0, %1i',x_moves_3(i)); end
fprintf(fileID,',');
if y_moves_3(i) < 0
fprintf(fileID,' %1i, 0',0-y_moves_3(i)); else
fprintf(fileID,' 0, %1i',y_moves_3(i)); end
if (num_steps ~= i)

fprintf(fileID,',');
end
end

fprintf(fileID,'};\n//Fin'); fprintf(fileID,'\n');
fclose(fileID);

type image_data.h
end

num_steps = 1290
long num_of_steps = 1290;

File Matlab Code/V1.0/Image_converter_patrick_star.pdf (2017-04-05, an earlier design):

clc
clear all
close all

Im_name = 'custom.png';
Im = imread(Im_name);
Im_size(:)=size(Im);%Gather size data of image X=Im_size(1);%Save the x dimension Y=Im_size(2);%Save the Y dimension

while Y > 300
Im = imresize(Im,.5);
Im_size(:)=size(Im);%Gather size data of image X=Im_size(1)%Save the x dimension Y=Im_size(2)%Save the Y dimension
end

X = 450
Y = 540
X = 225
Y = 270

histogram(Im)


%Add or remove thresholds in the line below according to the histogram %Globe threshs: 0,117,200
thresh = [117,200]


thresh =

117 200

%Convert the image based on the thresholds Im_Shaded = imquantize(Im,thresh);

%fileID = fopen('Untitled.txt','wt'); %fprintf(fileID,'%f',Im_Shaded); %fclose(fileID);

imshow(Im);

histogram(Im)

histogram(Im_Shaded)


imshow(Im_Shaded,[])

%Now isolating each shade as a seperate b and w image max_value=max(Im_Shaded(:))

max_value = 3

Im_array_1=im2bw(Im,thresh(1)/255); Im_array_2=~im2bw(Im,thresh(2)/255); Im_array_3=im2bw(Im,thresh(2)/255);

imshow(Im_array_1);


imshow(Im_array_2);

imshow(Im_array_3);


%-------------------------------------------num_objects_1 = max(max(bwlabel(Im_array_1)))

num_objects_1 = 1

num_objects_2 = max(max(bwlabel(Im_array_2)))

num_objects_2 = 5

num_objects_3 = max(max(bwlabel(Im_array_3)))

num_objects_3 = 4

%Converts the different shades into outlines
Im_array_outline_3 = bwmorph(Im_array_3,'remove');
Im_array_outline_2 = (bwmorph(bwmorph(Im_array_2,'remove'),'clean'));
Im_array_outline_1 = bwmorph(Im_array_1,'remove')-bwmorph(Im_array_3,'remove')-bwmorph(Im_array_2,'remove');

imshow(Im_array_outline_1)


Im_array_rot_1 = imrotate(Im_array_outline_1,270);
[x_moves, y_moves, x_coor, y_coor, X_1, Y_1] = image_2_machine(Im_array_rot_1,X,Y);

figure
plot(x_coor,y_coor)
grid on

Im_please_work = Im_array_1 - Im_array_3 - Im_array_outline_2;

imshow(Im_please_work)


Im_array_rot_1 = imrotate(Im_please_work,270);
[x_moves_2, y_moves_2, x_coor_2, y_coor_2, X_2, Y_2] = image_2_machine(Im_array_rot_1,X_1,Y_1);

figure
plot(x_coor_2,y_coor_2)
grid on


imshow(Im_array_outline_2)

Im_array_rot_2 = imrotate(Im_array_outline_2,270); if (Im_name ~= 'custom.png')

[x_moves_3, y_moves_3, x_coor_3, y_coor_3, X_3, Y_3] = image_2_machine(Im_array_rot_2,X_2,Y_2); else
[x_moves_3, y_moves_3, x_coor_3, y_coor_3, X_3, Y_3] = image_2_machine(Im_array_rot_2,1,1); end

figure
plot(x_coor_3,y_coor_3)
grid on


Im_please_work_2 = Im_array_2-Im_array_1;

imshow(Im_please_work_2)


Im_array_rot_2 = imrotate(Im_please_work_2,270);
[x_moves_4, y_moves_4, x_coor_4, y_coor_4, X_4, Y_4] = image_2_machine(Im_array_rot_2,X_3,Y_3);

figure
plot(x_coor_4,y_coor_4)
grid on dec2bin(abs(y_moves_3(1)),8);

%[x_move_3, y_move_3, final_x_3, final_y_3, num_steps_3 ] = conv_to_moves( Im_array_outline_1, final_x_2, final_y_2);

if (Im_name ~= 'custom.png')
num_steps = length(x_moves_4)+length(x_moves_3)+length(x_moves_2)+length(x_moves)

fileID = fopen('image_data.h','w');
fprintf(fileID,'long num_of_steps = ');
fprintf(fileID,'%1i;\n\n',num_steps);
fprintf(fileID,'//Coordinates: \n//'); for i = 1:length(x_coor_3)
if x_coor_3(i) < 0
fprintf(fileID,'%1i',0-x_coor_3(i)); else
fprintf(fileID,'%1i',x_coor_3(i)); end
fprintf(fileID,',');
if y_coor_3(i) < 0
fprintf(fileID,'%1i',0-y_coor_3(i)); else
fprintf(fileID,'%1i',y_coor_3(i)); end
if (num_steps ~= i)

fprintf(fileID,',');
end
end

fprintf(fileID,'\n//Move list from origin (0,0) with every 4 numbers being a step: \n//'); for i = 1:length(x_moves_3)
if x_moves_3(i) < 0
fprintf(fileID,' %1i, 0',0-x_moves_3(i));
else
fprintf(fileID,' 0, %1i',x_moves_3(i)); end
fprintf(fileID,',');
if y_moves_3(i) < 0
fprintf(fileID,' %1i, 0',0-y_moves_3(i)); else
fprintf(fileID,' 0, %1i',y_moves_3(i)); end
if (num_steps ~= i)

fprintf(fileID,';');
end
end
fprintf(fileID,'\n//Binary move list with 3 moves per byte\n//Format: 0x00,Move1,Move2,Move3\n//Example: 0x00110010 = 0x00,UR,DL,UL\n'); fprintf(fileID,'byte move_list[] = {');

write_2_file(x_moves_3,y_moves_3,fileID,1)
fprintf(fileID,'\n');
write_2_file(x_moves,y_moves,fileID,0) fprintf(fileID,'\n');
write_2_file(x_moves_2,y_moves_2,fileID,0) fprintf(fileID,'\n');
write_2_file(x_moves_4,y_moves_4,fileID,0) fprintf(fileID,'};');

fclose(fileID);

type image_data.h

else
num_steps = length(x_moves_3)

fileID = fopen('image_data.h','w'); fprintf(fileID,'long num_of_steps = '); fprintf(fileID,'%1i;\n\n',num_steps);

fprintf(fileID,'char move_list['); fprintf(fileID,'] = {');

for i = 1:num_steps
if x_moves_3(i) < 0
fprintf(fileID,' %1i, 0',0-x_moves_3(i)); else
fprintf(fileID,' 0, %1i',x_moves_3(i)); end
fprintf(fileID,',');
if y_moves_3(i) < 0
fprintf(fileID,' %1i, 0',0-y_moves_3(i)); else
fprintf(fileID,' 0, %1i',y_moves_3(i)); end
if (num_steps ~= i)

fprintf(fileID,',');
end
end

fprintf(fileID,'};\n//Fin'); fprintf(fileID,'\n');
fclose(fileID);

type image_data.h
end

num_steps = 1066
long num_of_steps = 1066;

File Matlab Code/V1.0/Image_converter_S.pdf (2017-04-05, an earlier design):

clc
clear all

Warning: No video frames were written to this file. The file may be invalid.

close all

Im_name = 'custom.png';
Im = imread(Im_name);
Im_size(:)=size(Im);%Gather size data of image X=Im_size(1);%Save the x dimension Y=Im_size(2);%Save the Y dimension

while Y > 300
Im = imresize(Im,.5);
Im_size(:)=size(Im);%Gather size data of image X=Im_size(1)%Save the x dimension Y=Im_size(2)%Save the Y dimension
end

X = 450
Y = 481
X = 225
Y = 241

histogram(Im)


%Add or remove thresholds in the line below according to the histogram %Globe threshs: 0,117,200
thresh = [117,200]

thresh =

117 200

%Convert the image based on the thresholds Im_Shaded = imquantize(Im,thresh);

%fileID = fopen('Untitled.txt','wt'); %fprintf(fileID,'%f',Im_Shaded); %fclose(fileID);

imshow(Im);


histogram(Im)


histogram(Im_Shaded)


imshow(Im_Shaded,[])

%Now isolating each shade as a seperate b and w image max_value=max(Im_Shaded(:))

max_value = 3

Im_array_1=im2bw(Im,thresh(1)/255); Im_array_2=~im2bw(Im,thresh(2)/255); Im_array_3=im2bw(Im,thresh(2)/255);

imshow(Im_array_1);


imshow(Im_array_2);


imshow(Im_array_3);


%-------------------------------------------num_objects_1 = max(max(bwlabel(Im_array_1)))

num_objects_1 = 1

num_objects_2 = max(max(bwlabel(Im_array_2)))

num_objects_2 = 19

num_objects_3 = max(max(bwlabel(Im_array_3)))

num_objects_3 = 1

%Converts the different shades into outlines
Im_array_outline_3 = bwmorph(Im_array_3,'remove');
Im_array_outline_2 = (bwmorph(bwmorph(Im_array_2,'remove'),'clean'));
Im_array_outline_1 = bwmorph(Im_array_1,'remove')-bwmorph(Im_array_3,'remove')-bwmorph(Im_array_2,'remove');

imshow(Im_array_outline_1)


Im_array_rot_1 = imrotate(Im_array_outline_1,270);
[x_moves, y_moves, x_coor, y_coor, X_1, Y_1] = image_2_machine(Im_array_rot_1,X,Y);

figure
plot(x_coor,y_coor)
grid on


Im_please_work = Im_array_1 - Im_array_3 - Im_array_outline_2;

imshow(Im_please_work)

Im_array_rot_1 = imrotate(Im_please_work,270);
[x_moves_2, y_moves_2, x_coor_2, y_coor_2, X_2, Y_2] = image_2_machine(Im_array_rot_1,X_1,Y_1);

figure
plot(x_coor_2,y_coor_2)
grid on


imshow(Im_array_outline_2)


Im_array_rot_2 = imrotate(Im_array_outline_2,270);
if (Im_name ~= 'custom.png')
[x_moves_3, y_moves_3, x_coor_3, y_coor_3, X_3, Y_3] = image_2_machine(Im_array_rot_2,X_2,Y_2); else
[x_moves_3, y_moves_3, x_coor_3, y_coor_3, X_3, Y_3] = image_2_machine(Im_array_rot_2,1,1); end

figure
plot(x_coor_3,y_coor_3)
grid on


Im_please_work_2 = Im_array_2-Im_array_1;

imshow(Im_please_work_2)

Im_array_rot_2 = imrotate(Im_please_work_2,270);
[x_moves_4, y_moves_4, x_coor_4, y_coor_4, X_4, Y_4] = image_2_machine(Im_array_rot_2,X_3,Y_3);

figure
plot(x_coor_4,y_coor_4)
grid on


dec2bin(abs(y_moves_3(1)),8);

%[x_move_3, y_move_3, final_x_3, final_y_3, num_steps_3 ] = conv_to_moves( Im_array_outline_1, final_x_2, final_y_2);

if (Im_name ~= 'custom.png')
num_steps = length(x_moves_4)+length(x_moves_3)+length(x_moves_2)+length(x_moves)

fileID = fopen('image_data.h','w');
fprintf(fileID,'long num_of_steps = ');
fprintf(fileID,'%1i;\n\n',num_steps);
fprintf(fileID,'//Coordinates: \n//'); for i = 1:length(x_coor_3)
if x_coor_3(i) < 0
fprintf(fileID,'%1i',0-x_coor_3(i)); else
fprintf(fileID,'%1i',x_coor_3(i)); end
fprintf(fileID,',');
if y_coor_3(i) < 0
fprintf(fileID,'%1i',0-y_coor_3(i)); else fprintf(fileID,'%1i',y_coor_3(i)); end
if (num_steps ~= i)

fprintf(fileID,',');
end
end

fprintf(fileID,'\n//Move list from origin (0,0) with every 4 numbers being a step: \n//'); for i = 1:length(x_moves_3)
if x_moves_3(i) < 0
fprintf(fileID,' %1i, 0',0-x_moves_3(i));
else
fprintf(fileID,' 0, %1i',x_moves_3(i)); end
fprintf(fileID,',');
if y_moves_3(i) < 0
fprintf(fileID,' %1i, 0',0-y_moves_3(i)); else
fprintf(fileID,' 0, %1i',y_moves_3(i)); end
if (num_steps ~= i)

fprintf(fileID,';');
end
end
fprintf(fileID,'\n//Binary move list with 3 moves per byte\n//Format: 0x00,Move1,Move2,Move3\n//Example: 0x00110010 = 0x00,UR,DL,UL\n'); fprintf(fileID,'byte move_list[] = {');

write_2_file(x_moves_3,y_moves_3,fileID,1)
fprintf(fileID,'\n');
write_2_file(x_moves,y_moves,fileID,0) fprintf(fileID,'\n');
write_2_file(x_moves_2,y_moves_2,fileID,0) fprintf(fileID,'\n');
write_2_file(x_moves_4,y_moves_4,fileID,0) fprintf(fileID,'};');

fclose(fileID);

type image_data.h

else
num_steps = length(x_moves_3)

fileID = fopen('image_data.h','w'); fprintf(fileID,'long num_of_steps = '); fprintf(fileID,'%1i;\n\n',num_steps);

fprintf(fileID,'unsigned char move_list['); fprintf(fileID,'] = {');

for i = 1:num_steps
if x_moves_3(i) < 0
fprintf(fileID,' %1i, 0',0-x_moves_3(i)); else
fprintf(fileID,' 0, %1i',x_moves_3(i)); end
fprintf(fileID,',');
if y_moves_3(i) < 0
fprintf(fileID,' %1i, 0',0-y_moves_3(i));

else
fprintf(fileID,' 0, %1i',y_moves_3(i)); end
if (num_steps ~= i)

fprintf(fileID,',');
end
end

fprintf(fileID,'};\n//Fin'); fprintf(fileID,'\n');
fclose(fileID);

type image_data.h
end

num_steps = 1040
long num_of_steps = 1040;

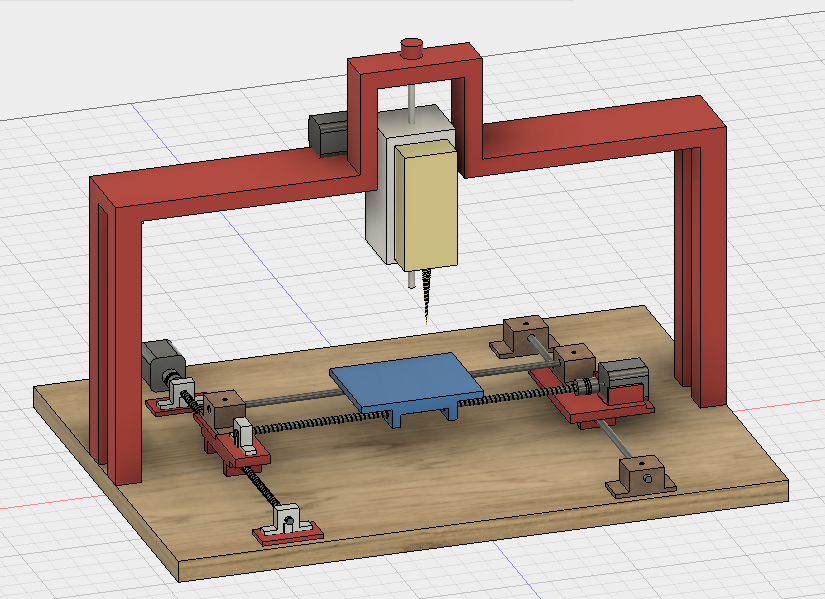
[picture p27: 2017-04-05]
Pictures/Model_v4_angle_1.png

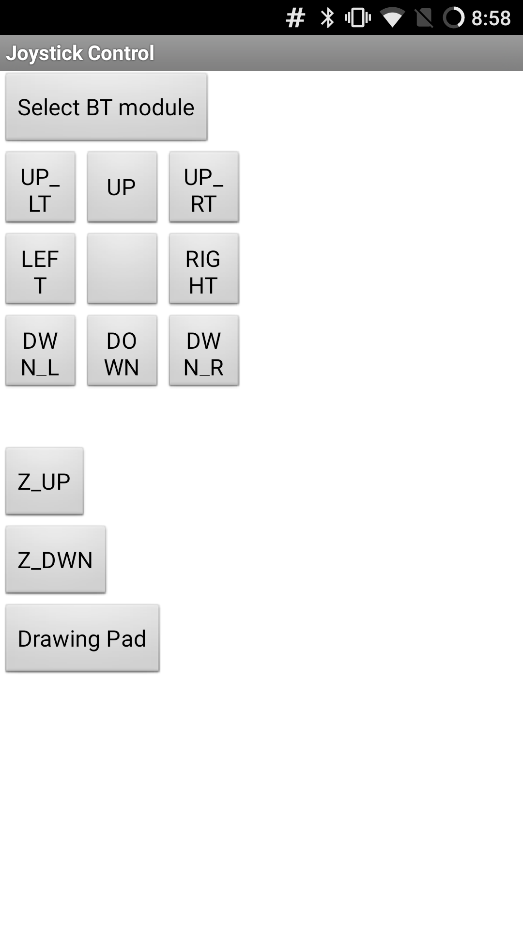
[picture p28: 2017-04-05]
Pictures/Screenshot_20170220-205812.png

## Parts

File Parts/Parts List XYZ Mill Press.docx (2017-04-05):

1. 3 Stepper Motors (x,y,z directions) https://www.amazon.com/gp/product/B00PNEQKC0/ref=oh_aui_detailpage_o03_s00?ie=UTF8&psc=1
2. Printer Railing
3. Conveyer Belt
4. 3 Arduinos
5. Mill Press
6. PVC pipe for the railing.

https://www.amazon.com/Stepper-Motor-Bipolar-64oz-Printer/dp/B00PNEQI7W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

https://www.amazon.com/Nema17-Stepper-Motor-4-lead-Connector/dp/B00QEXSCE8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

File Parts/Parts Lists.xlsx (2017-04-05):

Parts | Link | Price | Quantity | Who Bought
Stepper Motors | https://www.amazon.com/gp/product/B00PNEQKC0/ref=oh_aui_detailpage_o03_s00?ie=UTF8&psc=1 | $14.99 | 3 | Dineth(3)
Threaded Bar | https://www.amazon.com/gp/product/B01H1QNSAE/ref=oh_aui_detailpage_o05_s01?ie=UTF8&psc=1 | $16.98 | 4 | Chris(2)Steven(2)
Arduino Mega | https://www.amazon.com/gp/product/B00PD92EJ8/ref=oh_aui_detailpage_o00_s00?ie=UTF8&psc=1 | $11.89 | 1 | Steven
Linear Motion Bar | https://www.amazon.com/2-Pack-Linear-Motion-Length-Hardened/dp/B01I49ESN8 | $18.58 | 3 | Chris
Filament |  | $10 | 1
Arduino SD card reader | https://www.amazon.com/gp/product/B00SL0QWDU/ref=oh_aui_detailpage_o01_s00?ie=UTF8&psc=1 | $5.98 | 1 | Chris
RAMPs Board Kit | https://www.amazon.com/gp/product/B01CFJGHCI/ref=od_aui_detailpages00?ie=UTF8&psc=1 | $17.99 | 1 | Dineth
SD Card | https://www.amazon.com/gp/product/B00FM5E1EY/ref=oh_aui_detailpage_o00_s00?ie=UTF8&psc=1 | $5.40 | 2 | Chris
Linear Motion Sliders | https://www.amazon.com/CycleMore-SCS8UU-Linear-Bearing-Bushing/dp/B01A8G9U0G | $11.49 | 4 | Chris
End Stops | https://www.amazon.com/gp/product/B01CS82B8K/ref=oh_aui_detailpage_o01_s00?ie=UTF8&psc=1
Arcade Buttons

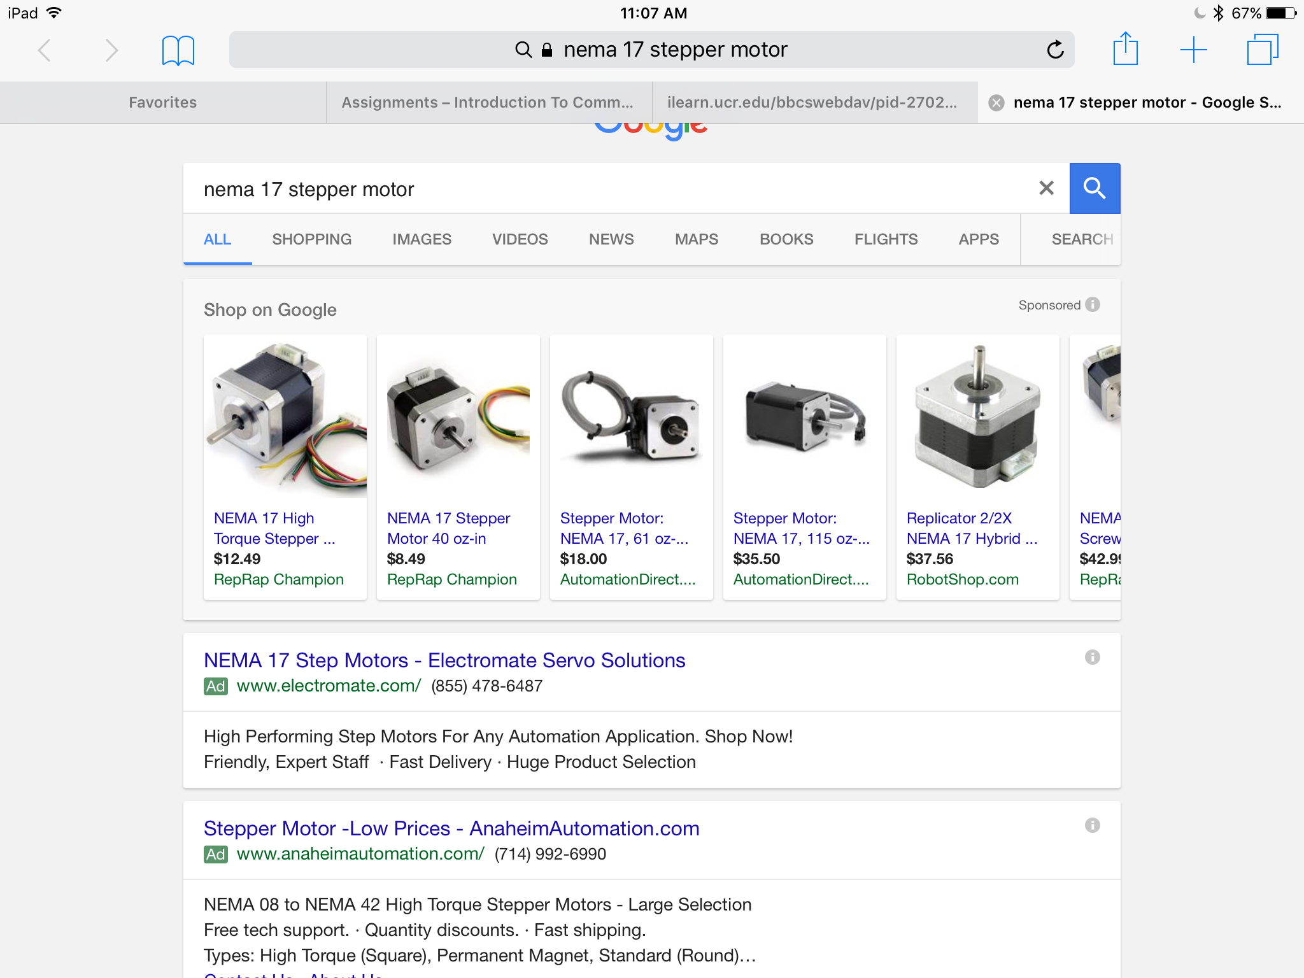
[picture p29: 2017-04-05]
Parts/File_000(1).png

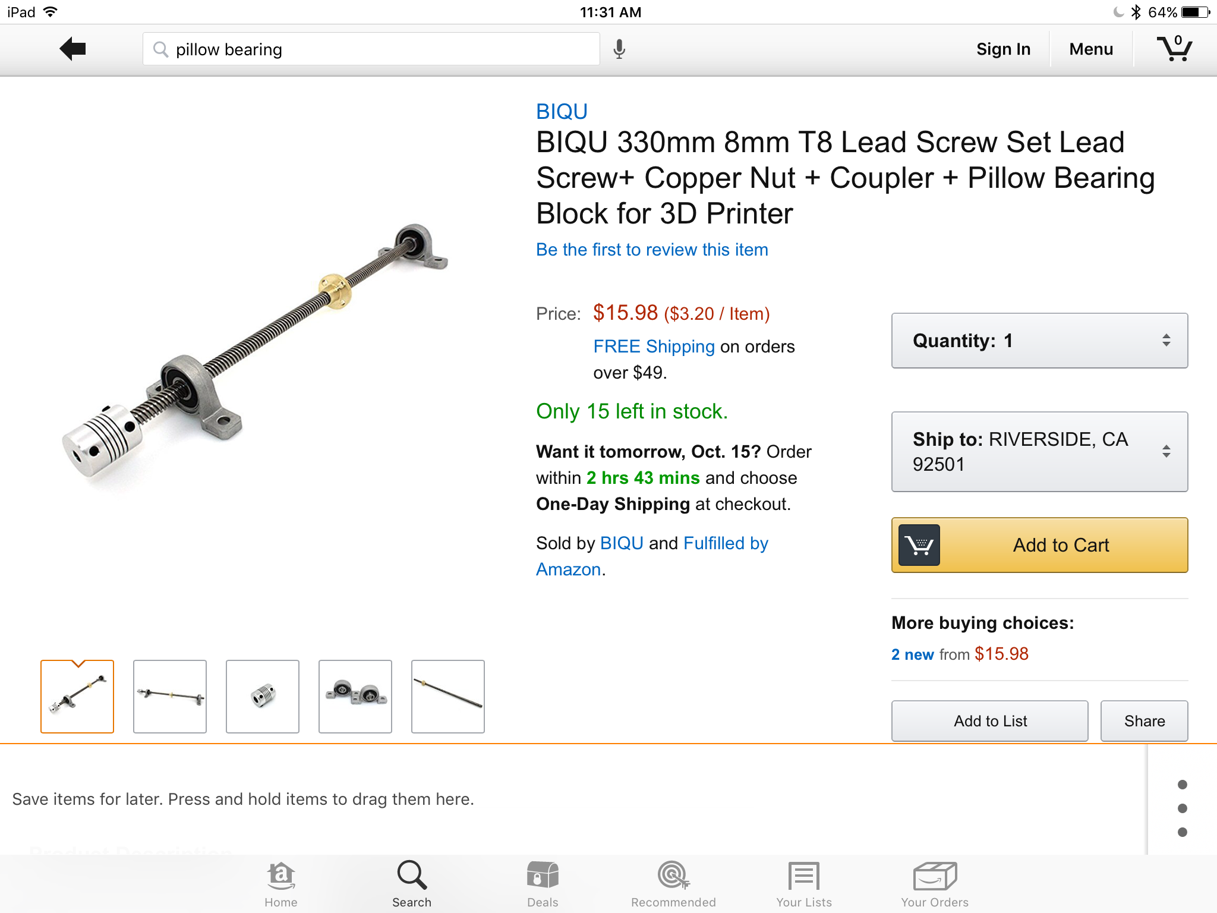
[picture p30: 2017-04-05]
Parts/File_003.png

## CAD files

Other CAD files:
Model Files/3D Mill Press v1.f3d
Model Files/CNC Machine v1.f3d

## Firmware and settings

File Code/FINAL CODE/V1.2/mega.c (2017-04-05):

#include "image_data.h"

// 0 - Hand Control, 1 - Image data, 2 - No calibration*beta*
int image_choice = 1;

int ht_chnge = 15;
int image_gain = 13;
char move_now = 1;
char drawing_image = 0;
int current_step = 0;
char image_done = 0;
char z_confirm = 0;
char point_check = 0;

char pen_down = 0;

String readString;

char automatic = 1;
int UD = 0;
int LR = 0;

int z_with_object_ht = 5000;
int reset_step = 0;

/* Arduino Micro output pins*/
int DWN = 27;
int UP = 29;
int LEFT = 31;
int RT = 33;
/* Arduino Micro Input Pins */
int IUP=59;//A5
int ILR=63;//A9

int MID = 33; // 33 mid point delta arduino, use 4 for attiny
int LRMID = 0;
int UPMID = 0;
char BTF = 0;


const int x_endstopPin_min = 3; // endstop for x-axis (min)
const int x_endstopPin_max = 2; // endstop for x-axis (max)

const int y_endstopPin_min = 14; // endstop for y-axis (min)
const int y_endstopPin_max = 15; // endstop for y-axis (max)

const int z_endstopPin_min = 18; // endstop for z-axis (min)
const int z_endstopPin_max = 19; // endstop for z-axis (max)

const int z_endstopPin_cal = 45; // endstop for z-axis (calibration)

const int buttonPin = 47; //D47    // the number of the pushbutton pin
const int buttonPin2 = 32; //D32
const int ledPin =  23;      // the number of the LED pin

int buttonState = 0;         // variable for reading the pushbutton status
int buttonState2 = 0;

int x_endstopvar_min = 0; //these states will contain value from reading input values
int x_endstopvar_max = 0;
int y_endstopvar_min = 0;
int y_endstopvar_max = 0;
int z_endstopvar_min = 0;
int z_endstopvar_max = 0;
int z_endstopvar_cal = 0;

char temperature_ready = 0;

////////////////////// COMMUNICATION VARIABLES //////////////////
int percentage_complete = 0;
int past_percentage = 0;

///////////////////////////////////////DELAY VARIABLES//////////////////////////////////////
int automatic_delay_speed = 700;
int manual_delay_speed = 500;

///////////////////////////////////////////INPUTS////////////////////////////////////
int XL = 0;
int XR = 0;
int YU = 0;
int YD = 0;
int ZU = 0;
int ZD = 0;

/////////////////////////////////////DIAMOND STUFF//////////////////////////////////
int XL1 = 1000;
int XR1 = 0;
int YU1 = 0;
int YD1 = 1000;
int ZU1 = 0;
int ZD1 = 0;

int XL2 = 0;
int XR2 = 1000;
int YU2 = 0;
int YD2 = 1000;
int ZU2 = 0;
int ZD2 = 0;

int XL3 = 1000;
int XR3 = 0;
int YU3 = 0;
int YD3 = 1000;
int ZU3 = 0;
int ZD3 = 0;

int XL4 = 0;
int XR4 = 1000;
int YU4 = 0;
int YD4 = 1000;
int ZU4 = 0;
int ZD4 = 0;

int XL5 = 0;
int XR5 = 1000;
int YU5 = 1000;
int YD5 = 0;
int ZU5 = 0;
int ZD5 = 0;

int XL6 = 1000;
int XR6 = 0;
int YU6 = 1000;
int YD6 = 0;
int ZU6 = 0;
int ZD6 = 0;

int XL7 = 0;
int XR7 = 1000;
int YU7 = 1000;
int YD7 = 0;
int ZU7 = 0;
int ZD7 = 0;

int XL8 = 1000;
int XR8 = 0;
int YU8 = 1000;
int YD8 = 0;
int ZU8 = 0;
int ZD8 = 0;

int XLEND = 0;
int XREND = 0;
int YUEND = 0;
int YDEND = 0;
int ZUEND = 0;
int ZDEND = 0;


int YUCount = 0;
int XRCount = 0;

//Demo pattern
int Done = 1;
int move_num = 0;
int printing = 0;

int readinput = 0;






/////////////////////////////////////////////// RESET FUNCTION //////////////////////////////////
int at_home = 0;
int running_reset = 0;
int reset = 0;
int actually_reset = 0;

void resetfunction()
{
  //Serial.println("Function called");
  //Serial.println(XR);
  if(at_home == 0 && running_reset == 0 && reset == 0)
  {
    running_reset = 1;
    //Serial.println("Reseting the platform...");
    Serial2.write(5);
    XL = 10000;
    YD = 10000;
    ZU = 10000;
  }
  else if (running_reset == 1 && at_home == 1)
  {
    //Serial.println("Platform reset\n");
    
    XL = 0;
    YD = 0;
    YU = 7000;
    XR = 1100;
    running_reset = 0;
    reset = 1;

  }
  
  return;
}

/////////////////////////////////////////////// CENTER FUNCTION //////////////////////////////////
int running_center = 0;
int centered = 0;
void centerfunction()
{
  //Serial.println("Function called");
  //Serial.println(XR);

    
    
    if (running_center == 0)
    {
      XR = 4000;
      YU = 4000;
      running_center =1;
      //Serial.println("Centering...");
      Serial2.write(7);
    }
    if (XR == 0 && YU == 0)
    {
      centered=1;
      running_center=0;
      //Serial.println("Centered\n");
      automatic = 0;
      Serial2.write(8);
      delay(500);
    }
  
  return;
}

/////////////////////////////////////////////// MOVER FUNCTION //////////////////////////////////
void mover()
{
  
  Done = 0;

    XL = XL1;
    XR = XR1;
    YU = YU1;
    YD = YD1;
    ZU = ZU1;
    ZD = ZD1;

    XL1 = XL2;
    XR1 = XR2;
    YU1 = YU2;
    YD1 = YD2;
    ZU1 = ZU2;
    ZD1 = ZD2;

    XL2 = XL3;
    XR2 = XR3;
    YU2 = YU3;
    YD2 = YD3;
    ZU2 = ZU3;
    ZD2 = ZD3;

    XL3 = XL4;
    XR3 = XR4;
    YU3 = YU4;
    YD3 = YD4;
    ZU3 = ZU4;
    ZD3 = ZD4;

    XL4 = XL5;
    XR4 = XR5;
    YU4 = YU5;
    YD4 = YD5;
    ZU4 = ZU5;
    ZD4 = ZD5;
    
    XL5 = XL6;
    XR5 = XR6;
    YU5 = YU6;
    YD5 = YD6;
    ZU5 = ZU6;
    ZD5 = ZD6;
    
    XL6 = XL7;
    XR6 = XR7;
    YU6 = YU7;
    YD6 = YD7;
    ZU6 = ZU7;
    ZD6 = ZD7;
    
    XL7 = XL8;
    XR7 = XR8;
    YU7 = YU8;
    YD7 = YD8;
    ZU7 = ZU8;
    ZD7 = ZD8;
    
    XL8 = XLEND;
    XR8 = XREND;
    YU8 = YUEND;
    YD8 = YDEND;
    ZU8 = ZUEND;
    ZD8 = ZDEND;
    move_num++;


  return;
}


void setup(){


 
  Serial.begin(9600);      // start serial communication at 9600bps
  Serial2.begin(9600);     // start serial1 communication at 9600bps

  

  
  pinMode(ledPin, OUTPUT);
  // initialize the pushbutton pin as an input:
  pinMode(buttonPin, INPUT);


  pinMode(x_endstopPin_min, INPUT);
  pinMode(x_endstopPin_max, INPUT);
  pinMode(y_endstopPin_min, INPUT);
  pinMode(y_endstopPin_max, INPUT);
  pinMode(z_endstopPin_min, INPUT);
  pinMode(z_endstopPin_max, INPUT);
  pinMode(z_endstopPin_cal, INPUT);
  
  pinMode(DWN, OUTPUT);
  pinMode(UP, OUTPUT);  
  pinMode(LEFT, OUTPUT); 
  pinMode(RT, OUTPUT);

   
  digitalWrite(DWN, HIGH);
  digitalWrite(UP, HIGH);
  digitalWrite(LEFT, HIGH);
  digitalWrite(RT, HIGH);
  
  //calabrate center
  LRMID = analogRead(ILR);
  UPMID = analogRead(IUP);

  pinMode(38, OUTPUT); //Enable X   // old 6
  pinMode(54, OUTPUT); //Step   X   // old 5
  pinMode(55, OUTPUT); //Direction // old 4


  pinMode(56, OUTPUT);// Enable Y
  pinMode(60, OUTPUT);// Step Y
  pinMode(61, OUTPUT);// Direction Y
  //digitalWrite(38,LOW);
  
  pinMode(62, OUTPUT);// Enable Z
  pinMode(46, OUTPUT);// Step Z
  pinMode(48, OUTPUT);// Direction Z
  
}

void loop(){

  //Serial.println(automatic);

 buttonState = digitalRead(buttonPin);
  buttonState2 = digitalRead(buttonPin2);

  
  UD = analogRead(IUP);
  LR = analogRead(ILR);
  
  if (UD < (UPMID+60) && (UD > (UPMID-60)))// original  = (UPMID-10)
      UD = UPMID;
  if (LR < (LRMID+60) && (LR > (LRMID-60)))
      LR = LRMID;
  
  //z-direction button UP
  int buttonvar = buttonState;
  int buttonvar2 = buttonState2;

  int x_endstopvar_min = digitalRead(x_endstopPin_min); //this obtains the "1" or "0" from endstop signal
  int x_endstopvar_max = digitalRead(x_endstopPin_max);
  int y_endstopvar_min = digitalRead(y_endstopPin_min);
  int y_endstopvar_max = digitalRead(y_endstopPin_max);
  int z_endstopvar_min = digitalRead(z_endstopPin_min);
  int z_endstopvar_max = digitalRead(z_endstopPin_max); 
  int z_endstopvar_cal = digitalRead(z_endstopPin_cal);

if(Serial2.available() > 0)
{
  readinput = Serial2.read();
  if(readinput == 20)
  {
    
    temperature_ready = 1;
//    Serial.println("--------");
//    Serial.println(temperature_ready);
//    Serial.println("--------");
  }
  else if(readinput == 21)
  {
    temperature_ready = 0;
//    Serial.println("--------");
//    Serial.println(temperature_ready);
//    Serial.println("--------");
  }
}

////////////////////RESET///////////////////////

if (!actually_reset)
{
if (!reset)
{
   resetfunction();
}

if ( XR == 0 && XL == 0 && YU == 0 && YD == 0 && reset && z_endstopvar_cal && reset_step == 0)
{
    ZU = 0;
    ZD = 10000;
    reset_step = 1;
}

if ( XR == 0 && XL == 0 && YU == 0 && YD == 0 && reset && !z_endstopvar_cal && reset_step == 1)
{
  ZU = 10000;
  XL = 1000;
  YD = 3000;
  ZD = 0;
  z_with_object_ht = 0;
  reset_step = 2;
}

if (YD == 0 && XR == 0 && reset_step == 2 && z_endstopvar_cal && !z_endstopvar_max && image_choice == 0)
{
  automatic = 0;
  ZD = 0;
  ZU = 0;
  actually_reset = 1;
  Serial2.write(127);
  delay(2000);
  Serial2.write(126);
}
else if (YD == 0 && XR == 0 && reset_step == 2 && z_endstopvar_cal && !z_endstopvar_max && image_choice == 1)
{
  automatic = 2;
  ZD = 0;
  ZU = 0;
  actually_reset = 1;
  Serial2.write(127);
}
}

if (z_confirm == 0 && automatic == 2 && buttonvar2 && actually_reset)
{
  z_confirm = 1;
  Serial2.write(8);
}

//Serial.println(temperature_ready);

if (z_confirm && automatic == 2 && buttonvar && actually_reset && temperature_ready)
{
  automatic = 1;
}
  

///////////////////////AUTO-IMAGE DRAWING/////////////////////////////
if (!z_endstopvar_max && !y_endstopvar_max && percentage_complete == 250  && automatic)
{
      
      delay(2000);
      Serial.println("Here");
      automatic = 0;
      ZU = 0;
      YD = 0;
      Serial2.write(126);
}

if (actually_reset && image_choice == 1 && drawing_image == 0 && image_done == 0 && automatic == 1)
{
  drawing_image = 1;
  current_step = sizeof(move_list)/4;
  z_with_object_ht = z_with_object_ht +ht_chnge;
        ZD = 300;
        //pen_down = 1;
        //Serial.println(pen_down);
}

if (drawing_image && XR == 0 && XL == 0 && YU == 0 && YD == 0 && image_done == 0)
{
    
    XL1 = image_gain*move_list[(num_of_steps-current_step)*4];
    XR1 = image_gain*move_list[((num_of_steps-current_step)*4)+1];
    YD1 = image_gain*move_list[((num_of_steps-current_step)*4)+2];
    YU1 = image_gain*move_list[((num_of_steps-current_step)*4)+3];
    //Serial.println(XR1);
    if ((XL1 > image_gain || XR1 > image_gain || YD1 > image_gain || YU1 > image_gain) && pen_down && move_now && !point_check)
    {
      ZD = 0;
      ZU = 300;
      pen_down = 0;
      move_now = 0;
      //Serial.println(ZU);
      
    }
    else if ((XL1 > image_gain || XR1 > image_gain || YD1 > image_gain || YU1 > image_gain) && !pen_down && move_now && !point_check)
    {
       ZD = 300;
       ZU = 0;
       pen_down = 1;
       point_check = 1;
    }
    else if ((XL1 > image_gain || XR1 > image_gain || YD1 > image_gain || YU1 > image_gain) && pen_down && move_now && point_check)
    {
       ZD = 0;
       ZU = 300;
       move_now = 0;
       pen_down = 0;
       point_check = 0;
    }
    else if (!pen_down && move_now)
    {
       ZD = 300;
       ZU = 0;
       move_now = 0;
       pen_down = 1;
    }
    else
      move_now = 0;
    
    if (ZD == 0 && ZU == 0 && move_now == 0)
    {
      move_now = 1;
      XL = XL1;
      XR = XR1; 
      YU = YU1;
      YD = YD1;
      current_step--;
    }

        
    percentage_complete = (100 - ((float(current_step) / float(num_of_steps))*100) + (150));
    
    
    if((percentage_complete != past_percentage) && (percentage_complete > 150) && (percentage_complete % 2))
    {
      if ((percentage_complete-150) < 5 || (percentage_complete-150) > 14)
      {
        Serial2.write(percentage_complete);
      }
      //Serial.println(percentage_complete);
      past_percentage = percentage_complete;
    }
    else if (percentage_complete == 250)
    {
      drawing_image = 0;
      image_done = 1;
      ZD = 0;
      ZU = 400;
      YD = 9000;
      percentage_complete = 250;
      Serial.println("Finish");
      Serial2.write(percentage_complete);
      drawing_image = 2;
      automatic_delay_speed = 500;
      z_with_object_ht = z_with_object_ht - ht_chnge;
    }
}




//Serial.println(automatic);





  
// RELAY SWITCH CODE //
///////////////////////////////////BLUETOOTH BEGIN/////////////////////////////////
  while (Serial.available()) {
    delay(3);  
    char c = Serial.read();
    readString += c; 
  }


if (readString.length() >0) {
    Serial.println(readString);
    
    if(readString == "UP")
    {
      BTF = 1;
    }
    else if(readString == "DOWN")
    {
      BTF = 2;
    }
    else if(readString == "LEFT")
    {
      BTF = 4;
    }
    else if(readString == "RIGHT")
    {
      BTF = 3;
    }
    else if(readString == "DR")
    {
      BTF = 5;
    }
    else if(readString == "DL")
    {
      BTF = 6;
    }
    else if(readString == "UR")
    {
      BTF = 7;
    }
    else if(readString == "UL")
    {
      BTF = 8;
    }
    else if(readString == "ZUP")
    {
      BTF = 9;
    }
    else if(readString == "ZDOWN")
    {
      BTF = 10;
    }
    else if(readString == "LIGHT")
    {
      automatic_delay_speed = 300; //faster motor speed --> lighter shade
    }
    else if(readString == "MEDIUM")
    {
      automatic_delay_speed = 500; //use standard delay speed for medium
    }
    else if(readString == "DARK")
    {
      automatic_delay_speed = 800; //slower motor speed --> darker shade
    }
    else if (readString == "off")
    {
      BTF = 0;
    }
    
    
    readString="";
  }

  //Serial.println(z_endstopvar_cal);

if ((x_endstopvar_min == 0) && (y_endstopvar_max == 0))
{
  at_home = 1;
}

else if ((x_endstopvar_min == 1) || (y_endstopvar_max ==1))
{
  at_home = 0;
}  

if (automatic)
{
if ( !z_endstopvar_min || !z_endstopvar_cal || z_with_object_ht == 0 )
{
  ZD = 0;
}
else if (!z_endstopvar_max)
{
  ZU = 0;
}
else if (!y_endstopvar_max)
{
  YD = 0;
}
else if (!y_endstopvar_min)
{
  YU = 0;
}
else if (!x_endstopvar_min)
{
  XL = 0;
}
else if (!x_endstopvar_max)
{
  XR = 0;
}
}
//////////////////???CENTERING CODE/////////////////////////////
/*
  if ((Done && (move_num < 9) && centered) && temperature_ready)
  {
    //Serial.println("yes");
    if (!printing)
    {
      
      //Serial.println("Drawing the diamonds...");
      Serial2.write(9);
    }
   
   mover();
   
   printing = 1;
  }
 */
 
  if ( XR == 0 && XL == 0 && YU == 0 && YD == 0 && printing)
  {
    
    Done = 1;
    if (move_num == 9 && printing)
    {
      printing = 0;
      automatic = 0;
      //Serial.println("Diamonds complete.\n");
      Serial2.write(10);
    }
  }


////////////////////////Automatic control///////////////////////
 if(automatic == 1)
  {
    
    if (ZU > 0 && z_endstopvar_max) 
{
    // turn LED on:
  z_with_object_ht++;
   digitalWrite(48,LOW);//direction
   digitalWrite(46,HIGH);//step
   digitalWrite(46,LOW);//step
   ZU--;
} 

else if(!buttonvar)
{
   digitalWrite(46,LOW);
}

if (ZD > 0 && z_endstopvar_min && z_endstopvar_cal && z_with_object_ht > 0) 
{
  z_with_object_ht--;
    // turn LED on:
   digitalWrite(ledPin, HIGH);
  // Serial.println("LED on");
    
   digitalWrite(48,HIGH);//direction
   digitalWrite(46,HIGH);//step
   digitalWrite(46,LOW);//step   
   ZD--;
   //pen_down = 1;
   //delayMicroseconds(200);
}  

 else if(!buttonvar/* || !buttonvar2*/)
{
   digitalWrite(46,LOW);
} 

  // y-direction UP
  if((((YU > 0)) && y_endstopvar_min ) && (readinput == 0  || readinput == 20) /*&& move_now*/){
   digitalWrite(DWN, LOW);
   digitalWrite(61,LOW);
   digitalWrite(UP, LOW);
   digitalWrite(60,HIGH);
   //delayMicroseconds(200);
   YUCount++;
   YU--;
    }
  else
  {
   digitalWrite(DWN, HIGH);
   digitalWrite(60,LOW);
  }
  // y-direction DOWN
  if((((YD > 0) && y_endstopvar_max )) && (readinput == 0  || readinput == 20) /*&& move_now*/)
  {
    
   digitalWrite(UP, LOW);
   digitalWrite(61,HIGH);
   //digitalWrite(DWN, LOW);
   digitalWrite(60,HIGH);
   //delayMicroseconds(200);
   //YUCount--;
   YD--;
  }
  else
  {
   digitalWrite(UP, HIGH);
   digitalWrite(60,LOW);
  }
  // LEFT-RIGHT

  //x-direciton RIGHT
  if(((((XR > 0)) && x_endstopvar_max )) && (readinput == 0 || readinput == 20) /*&& move_now*/)
  {// min
   digitalWrite(55,HIGH);
   //digitalWrite(LEFT, LOW);// LEDS
   digitalWrite(54,HIGH);
   //delayMicroseconds(200);
   XRCount++;
   XR--;
  }
  else{
   digitalWrite(54,LOW);
   digitalWrite(LEFT, HIGH);
  }

  //x-direction LEFT
  if(((((XL > 0)) && x_endstopvar_min )) && (readinput == 0 || readinput == 20) /*&& move_now*/)
  {
   digitalWrite(55,LOW);
   //digitalWrite(RT, LOW);
   digitalWrite(54,HIGH);
   //delayMicroseconds(200);
   //XRCount--;
   XL--;
  }else{
   digitalWrite(54,LOW);
   digitalWrite(RT, HIGH);
  }
  delayMicroseconds(automatic_delay_speed);
  }
  else if (automatic == 0)
  {
 ///////////////////////// MANUAL CONTROl //////////

 if (((buttonvar) || (BTF == 9)) && z_endstopvar_max)
{
    // turn LED on:
   z_with_object_ht++;
   digitalWrite(48,LOW);//direction
   digitalWrite(46,HIGH);//step
   digitalWrite(46,LOW);//step
} 

else if(!buttonvar)
{
   digitalWrite(46,LOW);
}

if (((buttonvar2 || (BTF == 10)) && z_endstopvar_min && z_endstopvar_cal && z_with_object_ht > 0))
{
  z_with_object_ht--;
    // turn LED on:
   digitalWrite(ledPin, HIGH);
  // Serial.println("LED on");
    
   digitalWrite(48,HIGH);//direction
   digitalWrite(46,HIGH);//step
   digitalWrite(46,LOW);//step   
   //delayMicroseconds(200);
}  
 else
{
   digitalWrite(46,LOW);
} 
// y-direction UP
  if(((((UD > UPMID + MID) || ((BTF == 1) || (BTF == 7)|| (BTF == 8)))) && y_endstopvar_min )){
   digitalWrite(DWN, LOW);
   digitalWrite(61,LOW);
   digitalWrite(UP, LOW);
   digitalWrite(60,HIGH);
   //delayMicroseconds(200);
   YUCount++;
   YU--;
    }
  else
  {
   digitalWrite(DWN, HIGH);
   digitalWrite(60,LOW);
  }
  // y-direction DOWN
   if((((((UD < UPMID - MID) || ((BTF == 2) || (BTF == 5)|| (BTF == 6)) || (YD > 0)) && y_endstopvar_max ))))
  {
   digitalWrite(UP, LOW);
   digitalWrite(61,HIGH);
   //digitalWrite(DWN, LOW);
   digitalWrite(60,HIGH);
   //delayMicroseconds(200);
   //YUCount--;
   YD--;
  }
  else
  {
   digitalWrite(UP, HIGH);
   digitalWrite(60,LOW);
  }
  // LEFT-RIGHT

  //x-direciton RIGHT
  //if(((((LR < LRMID - MID) || (XR > 0)) && x_endstopvar_max )) && (temperature_ready))
  if((((((LR > LRMID + MID) || ((BTF == 3)|| (BTF == 5)|| (BTF == 7))) || (XR > 0)) && x_endstopvar_max )))
  {// min
    
   digitalWrite(55,HIGH);
   //digitalWrite(LEFT, LOW);// LEDS
   digitalWrite(54,HIGH);
   //delayMicroseconds(200);
   XRCount++;
   XR--;
  }
  else{
   digitalWrite(54,LOW);
   digitalWrite(LEFT, HIGH);
  }

  //x-direction LEFT
  //if(((((LR > LRMID + MID) || (XL > 0)) && x_endstopvar_min )) && (temperature_ready))
  if((((((LR < LRMID - MID) || (( BTF == 4 )|| (BTF == 6)|| (BTF == 8))) || (XL > 0)) && x_endstopvar_min )))
  {
   digitalWrite(55,LOW);
   //digitalWrite(RT, LOW);
   digitalWrite(54,HIGH);
   //delayMicroseconds(200);
   //XRCount--;
   XL--;
  }else{
   digitalWrite(54,LOW);
   digitalWrite(RT, HIGH);
  }
delayMicroseconds(manual_delay_speed);
  }

}

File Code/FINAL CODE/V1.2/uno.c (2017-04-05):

#include <LiquidCrystal.h>
#include <math.h>

int cal_com = 0;
int delay_me = 500;
int stateRelay = HIGH;
int inPin = 7;         // button
int outPin = 8;       // relay

int state = LOW;      // the current state of the output pin
int reading = LOW;           // the current reading from the input pin
int previous = LOW;    // the previous reading from the input pin

long time = 0;         // the last time the output pin was toggled
long debounce = 200;   // the debounce time, increase if the output flickers

byte smiley[8] = {
  B00000,
  B10001,
  B10001,
  B00000,  
  B11111,
  B10001,
  B01110,
};

byte winky[8] = {
  B00000,
  B00001,
  B11001,
  B00000,  
  B11111,
  B10001,
  B01110,
};

byte sady[8] = {
  B00000,
  B10001,
  B10001,
  B00000,  
  B01110,
  B10001,
  B10001,
};

byte fire1[8] = {
  0b01000,
  0b00100,
  0b00110,
  0b00101,
  0b01101,
  0b10001,
  0b10001,
  0b01110
};

byte fire2[8] = {
  0b00000,
  0b00100,
  0b00010,
  0b00010,
  0b00101,
  0b01001,
  0b01001,
  0b00110
};

byte fire3[8] = {
  0b00010,
  0b00100,
  0b01100,
  0b01010,
  0b10010,
  0b10001,
  0b10001,
  0b01110
};

byte fire4[8] = {
  0b00000,
  0b00010,
  0b00100,
  0b01010,
  0b01010,
  0b10001,
  0b10001,
  0b01110
};

int fire_num = 3;
int fire_num1 = 6;
int fire_num2 = 4;

byte diamond[8] = {
  0b00000,
  0b00000,
  0b00100,
  0b01010,
  0b10001,
  0b01010,
  0b00100,
  0b00000
};


int diamond_emoji = 0;

double Thermistor(int RawADC) 
{
  double Temp;
  Temp = log(10000.0*((1024.0/RawADC-1))); 
  Temp = 1 / (0.001129148 + (0.000234125 + (0.0000000876741 * Temp * Temp ))* Temp );
  Temp = Temp - 273.15;          
  Temp = (Temp * 9.0)/ 5.0 + 32.0; 
  return Temp;
}

int val;                
double temp;            

LiquidCrystal lcd(12,11,5,4,3,2);
int input = 0;
void setup()
{

  pinMode(inPin, INPUT);
  pinMode(outPin, OUTPUT);
  
  lcd.begin(16,2);
  lcd.clear();
  Serial.begin(9600);       //Start serial communication at 9600bps
  Serial.flush();
  lcd.createChar(0, smiley);
  lcd.createChar(1, winky);
  lcd.createChar(2,sady);
  lcd.createChar(3,fire1);
  lcd.createChar(4,fire2);
  lcd.createChar(5,fire3);
  lcd.createChar(6,fire4);
  lcd.createChar(7,diamond);
  pinMode(9, OUTPUT);
  digitalWrite(outPin, stateRelay); //initialize relay to 0 at start of program
  
}

int not_con_LED = 1;
int input_old = 0;

void loop()
{
    
        
        val=analogRead(0);      
        temp=Thermistor(val);  

        // send data only when you receive data:
        if (Serial.available() > 0) 
        {
                // read the incoming byte:
               input = Serial.read();
               
               digitalWrite(9,HIGH);
        }

        
     //if (input != input_old)
     //{
     
        if(input == 0)
        {
          if(not_con_LED){
            digitalWrite(9,HIGH);
            not_con_LED=0;
            lcd.clear();
            lcd.print("Printer is  ");
            lcd.print(temp);
          lcd.print((char)223);
          lcd.print("F");
            lcd.setCursor(0, 1);
            lcd.print("powering on ");
            lcd.write(byte(1));
          }
          else 
          {
            digitalWrite(9,LOW);
            not_con_LED =1;
            lcd.clear();
            lcd.print("Printer is  ");
            lcd.print(temp);
          lcd.print((char)223);
          lcd.print("F");
            lcd.setCursor(0, 1);
            lcd.print("powering on ");
            lcd.write(byte(0));
            

          }
        }
        if(input == 5)
        {
          lcd.clear();
          lcd.print("Calibrating");
          lcd.setCursor(0, 1);
          lcd.print("Platform");
          stateRelay = LOW;
          digitalWrite(outPin,stateRelay);// low means RELAY ON, HIGH means RELAY OFF
          //delay(200);
        }

        
        else if (input == 127)
        {
          
          if (cal_com < 5)
          {
          lcd.clear();
          lcd.print("Calibration");
          lcd.setCursor(0, 1);
          lcd.print("Complete");
          
          //digitalWrite(outPin,LOW);// low means RELAY ON, HIGH means RELAY OFF
          }
          
          else if (cal_com < 10)
          {
          lcd.clear();
          lcd.print("Raise Z screw ");
          }
          else if (cal_com < 13)
          {
          lcd.clear();
          lcd.print("Then press");
          lcd.setCursor(0, 1);
          lcd.print("the white button");
          }
          else if (cal_com > 13)
            cal_com = 5;
            
          cal_com++;
          //delay(200);
        }
        else if(input == 126) //manual mode calibration complete
        {
          lcd.clear();
          lcd.print("Manual Mode");
          lcd.setCursor(0, 1);
          lcd.print("Temp: ");
          lcd.print(temp);
          lcd.print((char)223);
          lcd.print("F");
        }
        else if(input == 101)
        {
          if(stateRelay == LOW)
          {
            stateRelay = HIGH;
            digitalWrite(outPin, stateRelay); //turn off relay
          }
          else if(stateRelay == HIGH)
          {
            stateRelay = LOW;
            digitalWrite(outPin, stateRelay); //turn on relay
          }
          input = 126; //display the manual mode screen and temperature
        }
        else if (input == 7)
        {
          lcd.clear();
          lcd.print("Centering...");
          //delay(200);
        }
        else if (input == 8)
        { 
          lcd.clear(); //sets relay on once it enters this loop
          lcd.print("Press blue button");//user presses blue button to confirm print
          lcd.setCursor(0, 1);
          lcd.write(byte(fire_num));
          lcd.write(byte(fire_num1));
          lcd.write(byte(fire_num2));
          //lcd.setCursor(0, 1);
          //lcd.print("Temp: ");
          lcd.print(temp);
          lcd.print((char)223);
          lcd.print("F");

          
          
          if (temp >= 90) //send handshake when temp reaches proper 
          {                //temp  
            Serial.write(20);
           
          
          }
           else if (state == LOW)
            {
                reading = 1; 
            }
          fire_num++;
          if (fire_num == 7)
          fire_num = 3;
          fire_num1++;
          if (fire_num1 == 7)
          fire_num1 = 3;
          fire_num2++;
          if (fire_num2 == 7)
          fire_num2 = 3;
          //delay(200);
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
